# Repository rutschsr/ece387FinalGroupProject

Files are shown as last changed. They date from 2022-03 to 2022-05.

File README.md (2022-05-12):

# HandWriting Robot
Final Group Project for ECE387

## Project Members:
Sam Rutschilling, Brendan Moran, Deeparshan Khadka, and Michael Mattingly

# Introduction:

Our project is a handwriting robot for labels, it is designed to use a pen to write names or other text on to a label. This is to make more personable labels that have more depth and texture more similar to handwriting than labels printed by traditional printers.

The printer has a 3D printed frame with two 3D printed "carriages" for each axis (X and Y). The carriages for each axis are driven by stepper motors similar to a 3D printer. The carriages move back and forth on smooth, rigid plastic tubes desiged for use with cake decorating. Gears are printed into the design of the main body and X-Axis carriage for the stepper motors to interface with.

The Y-axis carriage, which is mounted to the X-axis carriage, contains the mount for the pen. The pen is controlled using a small 9-gram servo. The servo moves a small block vertically to determine if the pen is in contact with the surface of the paper. The pen holder is mounted to the Y-axis carriage using brass standoffs. Brass Standoffs also allow the pen holder to move freely.

As a group we used a Trello board to keep track of what tasks needed done, which were in progress, and which still needed completed.

# 3D printed parts

The body and mechanical parts of the pritner are constructed of 3D printed parts. These 3D parts were designed collaboratively using the cloud features of Autodesk Fusion 360. All of the 3D parts used in this project are located in this [Folder](https://github.com/rutschsr/ece387FinalGroupProject/tree/main/3-D%20printed%20parts). After the parts were desgined in Fusion 360 they were exported into the  stereolithography (.stl) format to be used by the slicer ([Utlimaker Cura](https://ultimaker.com/software/ultimaker-cura)). A slicer in the context of 3D printing takes a 3D model and sperates it into each of the layers that can be printed by a 3D printer. It then exports these layers in machine "g-code" that give the 3D printer specific instructions on where to move and how to place material. All of the 3D printed parts were printed using white or black PLA (polycactic acid) as shown below.

PLA Filament

## Main Body

The main body of the printer is the largest piece of the project and includes several important design features. The first important design decision is the inclusion of a gap in the bottom of the frame, designed to allow the user to pass the piece of paper to be pritned through to the print area. The second important design detail is the inclusion of holes to hold the printer rods near the top. These were an important part to be 3D printed, as the 3D printing process allows keeping much more accurate dimensions than we could constructing by hand using materials such as wood. These are directly in line with each other so the rods stay parallel to each other. The final design detail that is important to note for this part, is the Gear located along the edge on one side. This was also the most difficult detail to include, as none of the members of our group are mechanical engineers and have little expierence modeling 3D parts the way it is. A Fusion 360 add on to produce rack gears helped with this process, however. 

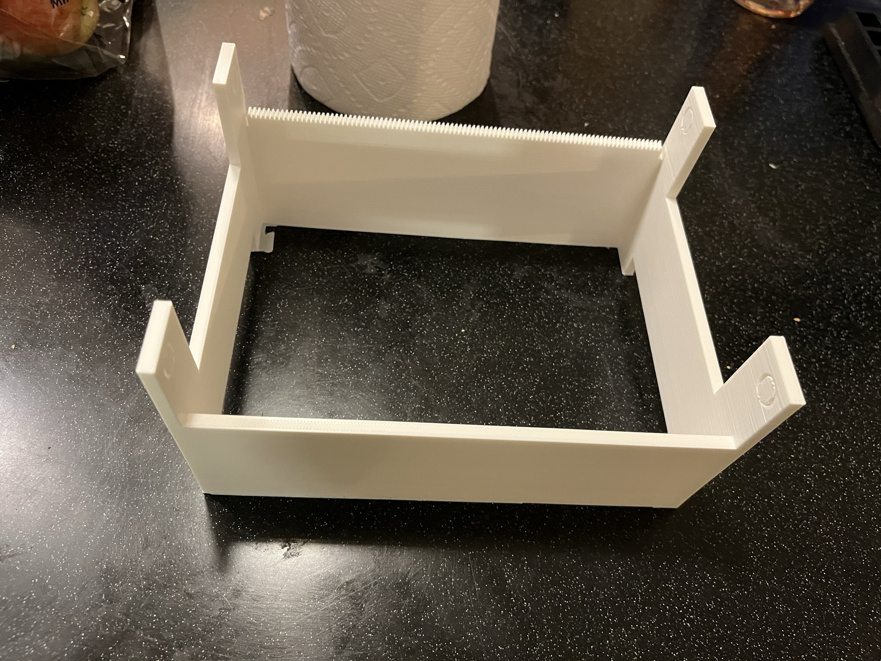
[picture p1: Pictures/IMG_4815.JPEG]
Main Body


## X-Axis Carriage

The X-Axis carriage is the next largest piece. The X-Axis carriage spans and slides on the cake rods supported by the main body. The X-Axis carriage also contains a mounting bracket for the stepper motor, and holes for more rods that the Y-Axis carriage mount to, as well as the gear for movement of the Y-Axis carriage.

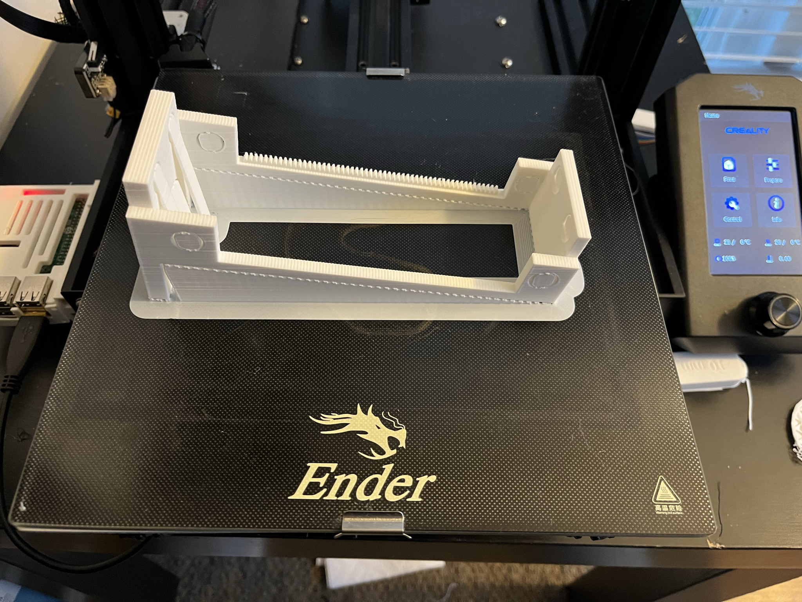
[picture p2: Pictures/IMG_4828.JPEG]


## Y-Axis Carriage

The Y-Axis Carriage is much more simple and smaller than the other pieces. It just contains holes for the rods supported by the X-Axis carriage and a mount for a stepper motor. The Servo mount attatchs to the bottom of the carriage using brass standoffs.

## Servo Mount

The Servo mount attatchs to the bottom of the Y-Axis carriage and contains a mounting bracket for the small 9g servo, as well as mounting holes for the brass standoffs that the pen bracket moves vertically along. This piece proved problamatic as in the first version of the part the mounting brackets for the servo were undersized and snapped off whenever attatching the servo motor was attempted. Simply increasing the size of the mounting brackets remedied this situation.

## Pen Bracket

The pen bracket is a very simple piece, it is just a block that contains properly spaced holes to slide on the brass standoffs attatched to the bottom of the Servo mount as well as a hole for the pen or marker to be attatched to. Additionally, it has a cutout on one side for the servo arm to interact with and move.

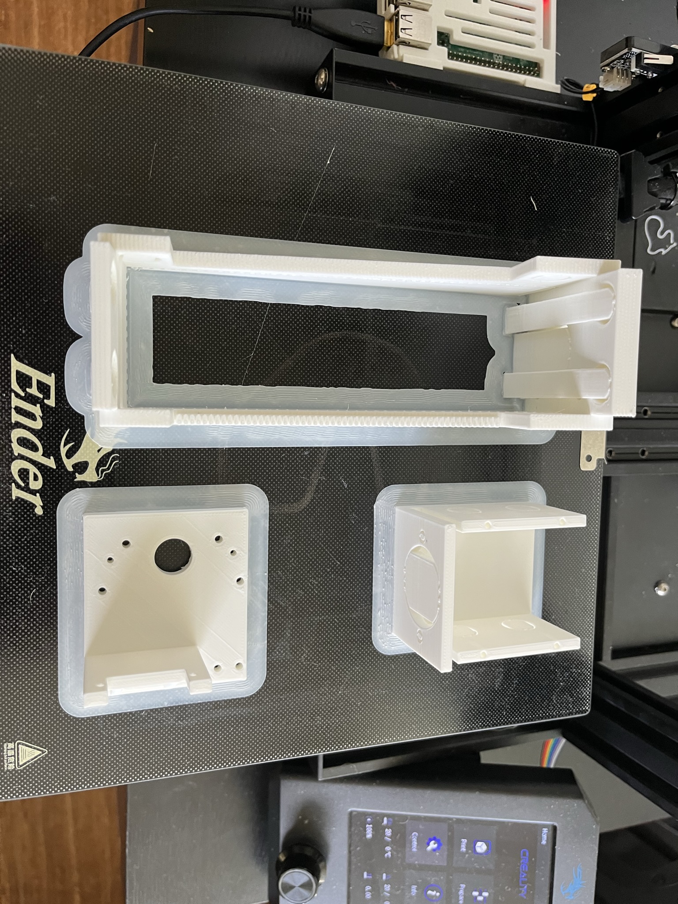
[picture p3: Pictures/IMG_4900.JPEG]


The image above shows a print with the X-Axis carriage, Y-Axis Carriage, and servo mount. These pieces had to be reprinted to correct issues with them.

## Gears

The gears were the most difficult 3D printed component to design, as no one in the group was quite sure how to start with them. Another Fusion 360 plugin helped to create the gears, and some trial and error was used to determine the best size to use.

# Electrical Parts

The electrical components of our robot consist of two steppers and a servo motor. Each carriage has a stepper mounted to it in order to move the pen horizontally and vertically. The servo is just used to extend and retract the pen. All three motors are controlled from a raspberry pi through its GPIO pins which allow us to employ pulse width modulation and four-channel stepping for driving the motors.

# Programming

Programming the robot to operate properly was just a matter of varying the speed at which one stepper moves in relation to the other. Steep diagonal movements, for example, can be achieved by stepping the y-axis motor twice for every single x-axis step. A more complicated motion such as a curve requires taking the equation of a circle and mapping a set of x coordinates to that function to produce the corresponding number of y-steps for every x-step.

# Demonstration

Img alt text (https://www.youtube.com/watch?v=LLpY4BQX6XM)

# Issues / Improvements

One of the issues was with the hole sizing for the X and Y axis carriages. These parts were designed with holes where the diameter matched exactly the diameter of the rods. This meant that the fit was tight and there was no room for the parts to move back and forth. This was fixed by increasing the diameter of the holes in the 3D model and reprinting the affected parts.

Another improvement we would have made had we had more time is to add the ability to type any arbitrary text into the unit to print. As of now the "hello World" as shown in the demonstration is hard coded.

# Cost

Cost breakdown. Costs for 3D printed parts are estimated from the slicer's estimate of the filament required for printing. Based on $22 per 1kg (335m) spool of 1.75mm PLA. 3D printed parts do not consider the price of electricity used to construct.

| Part | Quantity | Cost | Note |
| --- | --- | --- | --- |
| Main Body | 1 | $4.67 | PLA |
| X-Axis carriage | 1 | $1.28 | PLA |
| Y-Axis carriage  | 1 | $1.67 | PLA |
| Pen Mount | 2 | $3.13 | PLA |
| Servo | 2 | $5.49 |  |
| X-Axis Stepper| 2 | $13.99 |  |
| Y-Axis Stepper| 2 | N/A | Already Had |
| Limit Switches | 2 | $1.17 |  |
| Stepper Driver| 1 | $28.99|  |
| Raspberry Pi | 1 | |  |
| 3D printed Gears | 1 | $0.24 | PLA |
| Brass Standoffs | N/A | $14.99 |  |
| Cake Rods | 4 | $9.49 | Pack of 24 |

Total: $85.11

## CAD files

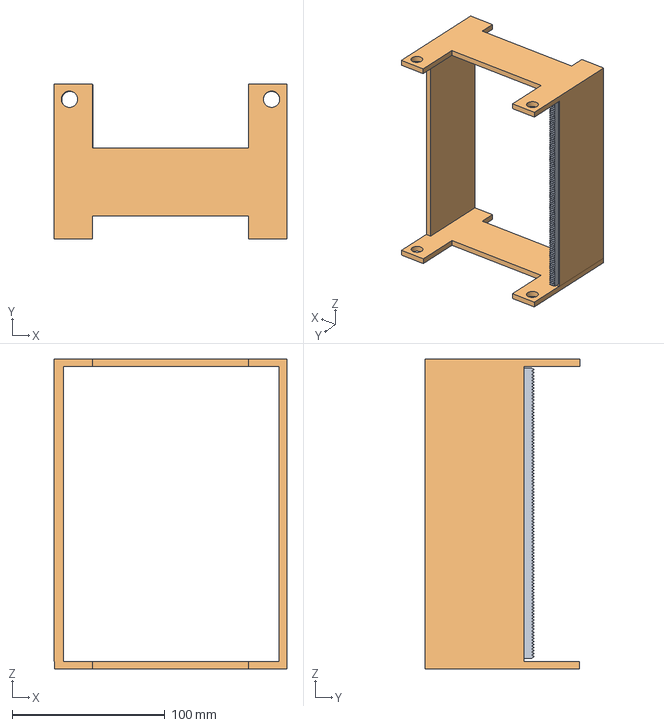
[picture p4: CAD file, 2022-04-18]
3-D printed parts/MainBody v5.step
152.4 x 101.6 x 203.0 mm

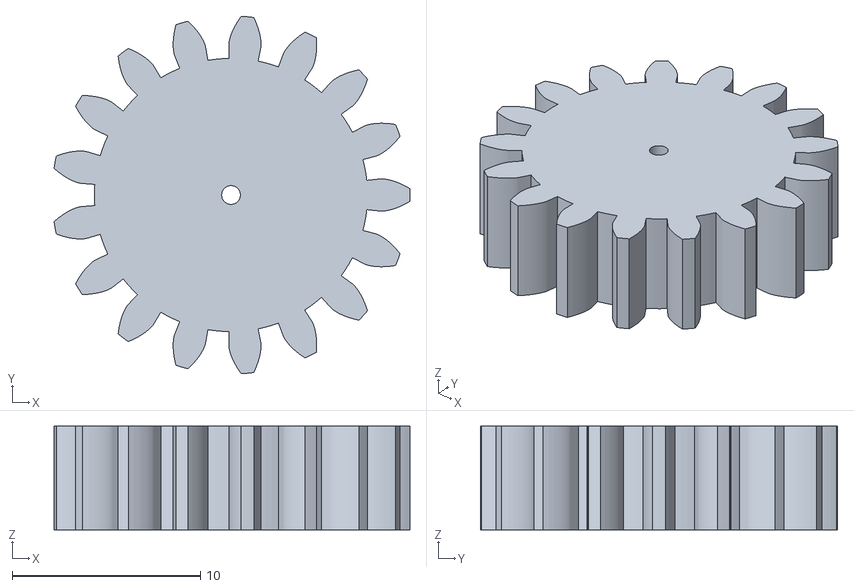
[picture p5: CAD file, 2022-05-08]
3-D printed parts/Gear v1.stl
18.9 x 19.0 x 5.50

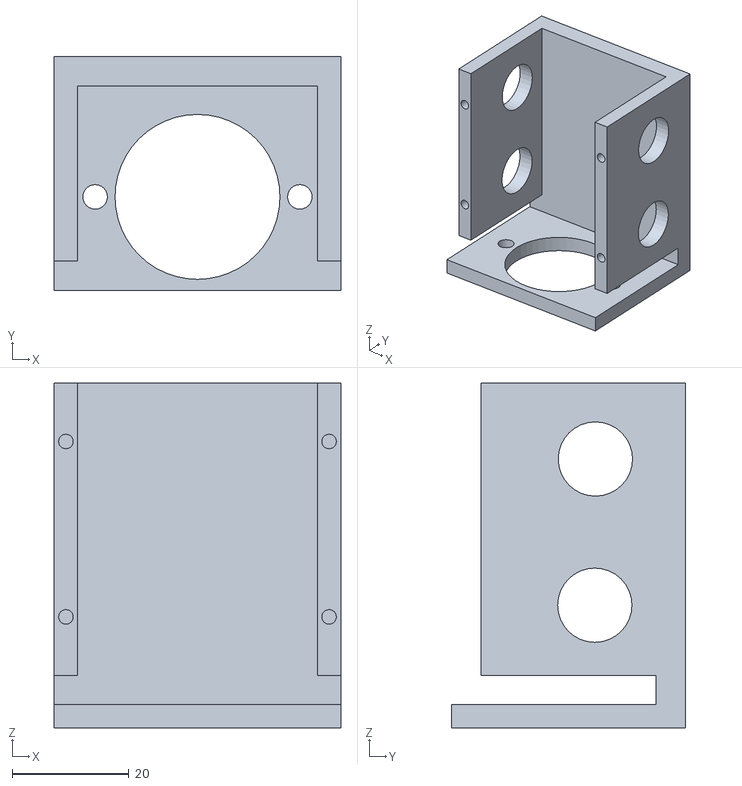
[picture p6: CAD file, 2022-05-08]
3-D printed parts/Y v7.stl
49.0 x 40.0 x 59.0

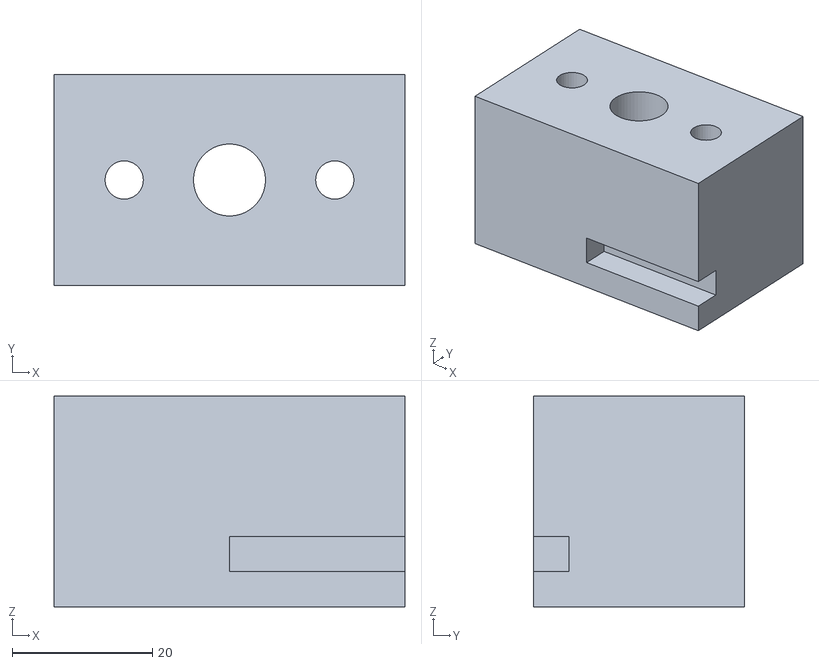
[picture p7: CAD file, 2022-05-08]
3-D printed parts/MarkerMount v1.stl
50.0 x 30.0 x 30.0

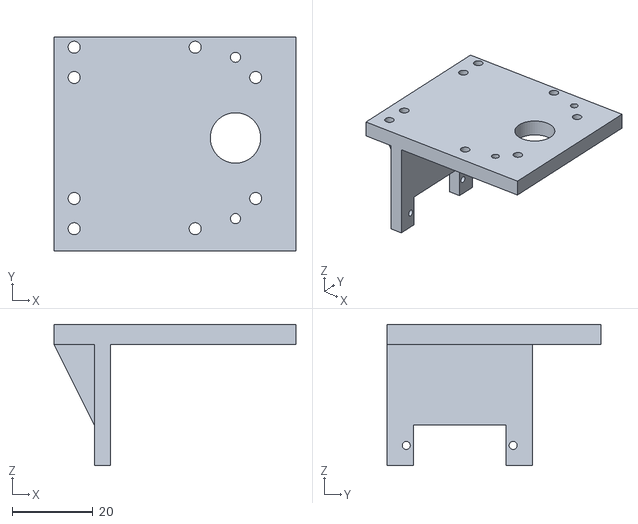
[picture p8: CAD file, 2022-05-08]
3-D printed parts/ServoMount v4.stl
60.0 x 53.0 x 35.0

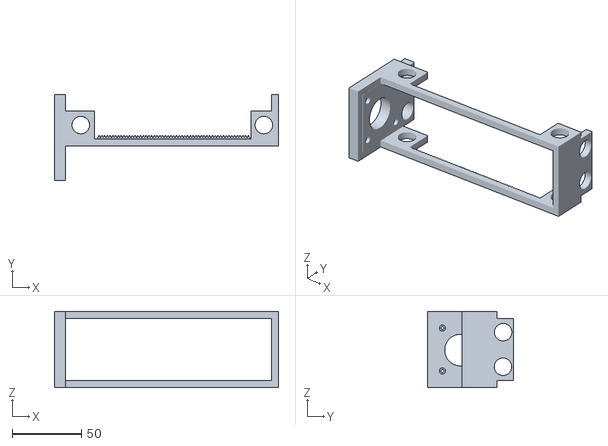
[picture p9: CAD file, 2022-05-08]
3-D printed parts/X v6.stl
162.0 x 62.0 x 55.0

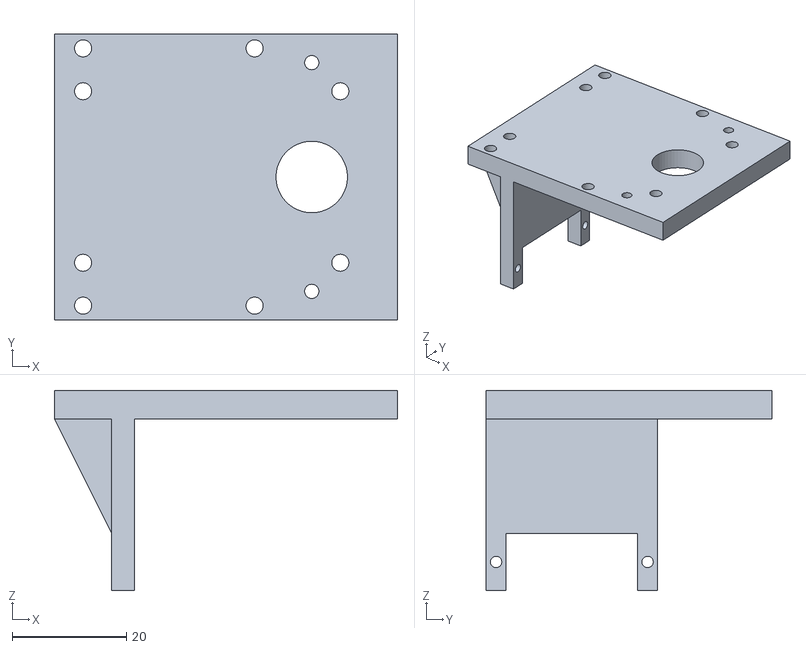
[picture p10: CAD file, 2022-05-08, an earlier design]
3-D printed parts/ServoMount v2.stl
60.0 x 50.0 x 35.0

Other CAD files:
3-D printed parts/X v5.step
3-D printed parts/Y v6.stl
3-D printed parts/X v4.stl
3-D printed parts/Gear v1.f3d
3-D printed parts/MainBody v5.f3d
3-D printed parts/MainBody v5.stl
3-D printed parts/MarkerMount v1.f3d
3-D printed parts/ServoMount v4.f3d
3-D printed parts/X v6.f3d
3-D printed parts/Y v7.f3d

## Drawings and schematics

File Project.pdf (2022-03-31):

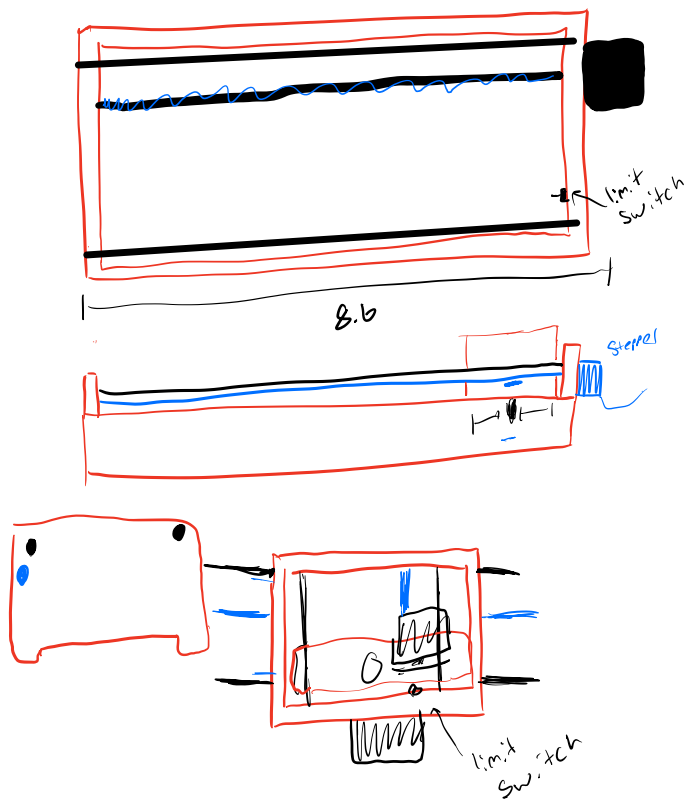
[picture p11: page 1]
Climfitch; iwi

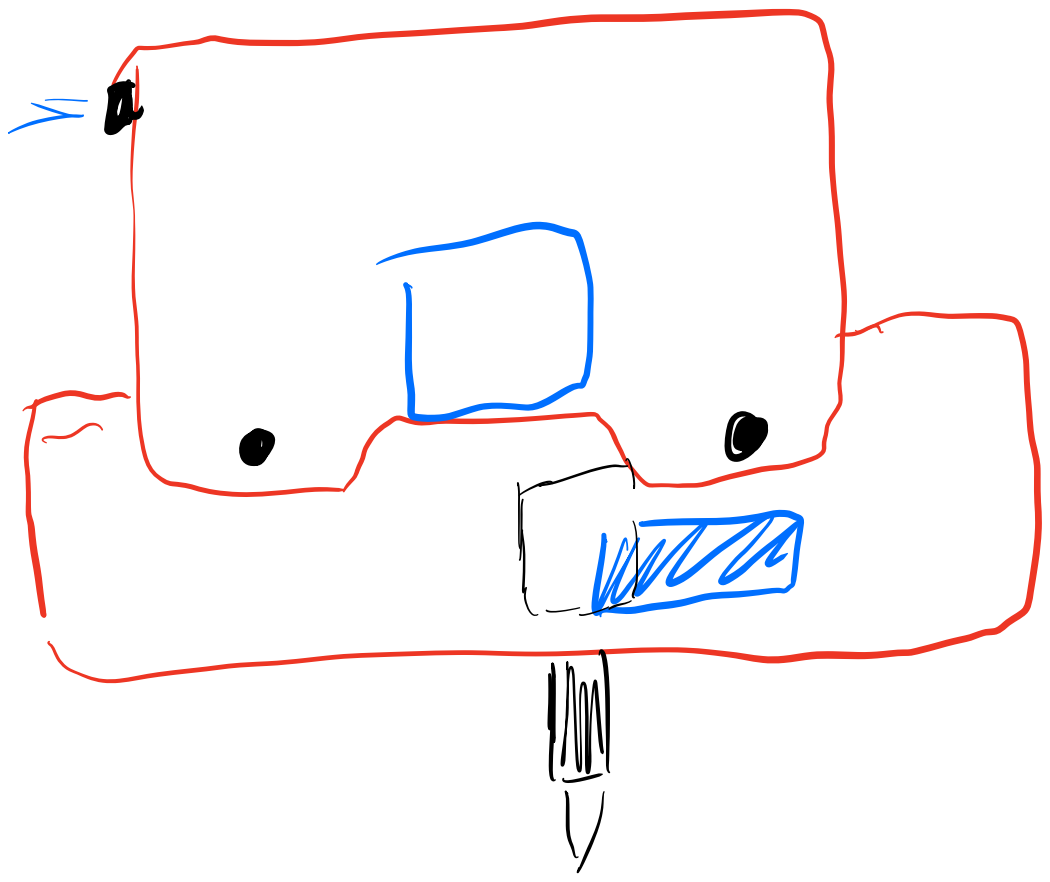
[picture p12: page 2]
Foi

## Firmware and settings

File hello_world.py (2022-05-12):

import RPi.GPIO as GPIO
from time import sleep
from math import sqrt

# halfstep advance sequence
adv = [ (1,0,0,1), (0,0,0,1), (0,0,1,1), (0,0,1,0),
        (0,1,1,0), (0,1,0,0), (1,1,0,0), (1,0,0,0)]

# halfstep reverse sequence
rev = [ (1,0,0,0), (1,1,0,0), (0,1,0,0), (0,1,1,0),
        (0,0,1,0), (0,0,1,1), (0,0,0,1), (1,0,0,1)]

# enable GPIO
GPIO.setmode(GPIO.BOARD)

# define the pins used for x and y steppers
stepper_x = (13, 11, 7, 5)
stepper_y = (8, 10, 12, 16)

# set the stepper pins to output
GPIO.setup(stepper_x, GPIO.OUT)
GPIO.setup(stepper_y, GPIO.OUT)

# initialize the steppers to 0 voltage
GPIO.output(stepper_x, 0)
GPIO.output(stepper_y, 0)

# set the servo pin to output and 50 Hz PWM frequency
GPIO.setup(19, GPIO.OUT)
servo = GPIO.PWM(19, 50)

# start the servo at rest
servo.start(0)

# function for extending the pen
def extend():
    servo.ChangeDutyCycle(9.5)
    sleep(0.2)
    servo.ChangeDutyCycle(0)

# function for retracting the pen
def retract():
    servo.ChangeDutyCycle(8)
    sleep(0.2)
    servo.ChangeDutyCycle(0)

# move upwards by n steps
def up(cycles):
    for _ in range(cycles):
        for step in range(8):
            GPIO.output(stepper_y, adv[step])
            sleep(0.0008)

# move downwards by n steps
def down(cycles):
    for _ in range(cycles):
        for step in range(8):
            GPIO.output(stepper_y, rev[step])
            sleep(0.0008)

# move left by n steps
def left(cycles):
    for _ in range(cycles):
        for step in range(8):
            GPIO.output(stepper_x, rev[step])
            sleep(0.0008)

# move right by n steps
def right(cycles):
    for _ in range(cycles):
        for step in range(8):
            GPIO.output(stepper_x, adv[step])
            sleep(0.0008)

# slant up and to the right n steps
def up_right(cycles):
    for _ in range(cycles):
        for step in range(16):
            GPIO.output(stepper_y, adv[step%8])
            if ((~step)&1):
                GPIO.output(stepper_x, adv[int(step/2)])
            sleep(0.0008)

# slant down and to the right n steps
def down_right(cycles):
    for _ in range(cycles):
        for step in range(16):
            GPIO.output(stepper_y, rev[step%8])
            if ((~step)&1):
                GPIO.output(stepper_x, adv[int(step/2)])
            sleep(0.0008)

# function for drawing the letter H
def draw_H():
    extend()
    up(320)
    retract()
    down(160)
    extend()
    right(160)
    retract()
    up(160)
    extend()
    down(320)
    retract()

# function for drawing the letter E
def draw_E():
    up(160)
    extend()
    right(160)
    retract()
    up(160)
    extend()
    left(160)
    down(320)
    right(160)
    retract()

# function for drawing the letter L
def draw_L():
    up(320)
    extend()
    down(320)
    right(160)
    retract()

# this is the equation for a quarter circle.
# it returns the difference in y-steps after each single x-step
def transform(val):
    curr = round(sqrt(1638400 - (val - 1280)**2))
    prev = round(sqrt(1638400 - (val - 1281)**2))
    return curr - prev

# map a series of x-steps to the corresponding number of y-steps 
# for a quarter circle
y_steps = [0] + list(map(transform, [i for i in range(1, 1280)]))

# function for drawing the letter O using four quarter circles
def draw_O():
    up(160)
    extend()
    current_y_step = 0
    for i in range(1000):
        GPIO.output(stepper_x, adv[i%8])
        sleep(0.0008)
        for _ in range(y_steps[i]):
            GPIO.output(stepper_y, adv[current_y_step])
            sleep(0.0008)
            current_y_step = (current_y_step + 1) % 8

    current_y_step = 0
    for i in range(1000):
        GPIO.output(stepper_x, adv[i%8])
        sleep(0.0008)
        for _ in range(y_steps[999-i]):
            GPIO.output(stepper_y, rev[current_y_step])
            sleep(0.0008)
            current_y_step = (current_y_step + 1) % 8
    left(40)
    current_y_step = 0
    for i in range(1000):
        GPIO.output(stepper_x, rev[i%8])
        sleep(0.0008)
        for _ in range(y_steps[i]):
            GPIO.output(stepper_y, rev[current_y_step])
            sleep(0.0008)
            current_y_step = (current_y_step + 1) % 8

    current_y_step = 0
    for i in range(1000):
        GPIO.output(stepper_x, rev[i%8])
        sleep(0.0008)
        for _ in range(y_steps[999-i]):
            GPIO.output(stepper_y, adv[current_y_step])
            sleep(0.0008)
            current_y_step = (current_y_step + 1) % 8
    retract()
    right(250)
    down(160)

# function for drawing the letter W
def draw_W():
    extend()
    down_right(160)
    up_right(60)
    down_right(60)
    up_right(140)
    retract()
    down(300)

# function for drawing the letter R
def draw_R():
    extend()
    up(320)
    right(160)
    down(160)
    left(180)
    right(40)
    down_right(80)
    retract()
    right(40)

# function for drawing the letter D
def draw_D():
    extend()
    up(320)
    current_y_step = 0
    for i in range(1280):
        GPIO.output(stepper_x, adv[i%8])
        sleep(0.0008)
        for _ in range(y_steps[1279-i]):
            GPIO.output(stepper_y, rev[current_y_step])
            sleep(0.0008)
            current_y_step = (current_y_step + 1) % 8
    
    current_y_step = 0
    for i in range(1280):
        GPIO.output(stepper_x, rev[i%8])
        sleep(0.0008)
        for _ in range(y_steps[i]):
            GPIO.output(stepper_y, rev[current_y_step])
            sleep(0.0008)
            current_y_step = (current_y_step + 1) % 8
    left(20)
    retract()
    right(160)

# sequence of letters to write "HELLO WORLD!"
draw_H()
right(40)
draw_E()
right(40)
draw_L()
right(40)
draw_L()
draw_O()
left(1000)
down(40)
draw_W()
right(20)
draw_O()
right(40)
draw_R()
right(60)
draw_L()
right(40)
draw_D()
right(40)
extend()
up(40)
retract()
up(40)
extend()
up(240)

servo.stop(0)
GPIO.cleanup()

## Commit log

2022-04-18 3-D printed parts
    [MainBody v5.step, MainBody v5.stl, X v4.stl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]
2022-05-08 Add all 3d printed parts
    [Gear v1.f3d, Gear v1.stl, MainBody v5.f3d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]
